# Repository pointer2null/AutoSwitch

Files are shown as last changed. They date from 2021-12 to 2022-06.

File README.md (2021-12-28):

# AutoSwitch

Auto switch to start a vac or dust collector when a tool starts.

Simple circuit based on the ATTiny85 PCU that monitors the current drawn by a tool, typically a wood working tool such as a saw or planer, and activates a dust collecter when that tool is switched on.

Current is sensed with the ACS712 hall device and the ATTiny85 samples this and after a short delay fires the triac, via an opto isolator, to power on the dust collector.

A seperate relay provides a volt free set of contacts in case blast gates need controlling.

There is a serial port which allows tweaking of the trigger values and time delays.

## Operation

The AtTiny85 uses it's onboard DAC to sample the analogue output from the hall sensor. If this value is above the adcThreshold value, a counter is incremented on each poll, up to the max counter value. If the hall value is below this threshold the counter is decremented. When the counter exceed the on count value and the hall value is above the threadhold, the output triac is switched on. When the count drops below the off count value and the hall value is below the threashold, the triac is switched off. To give a clean shutoff the count value is also set to zero at this point.

## Serial interface

A vac switch doesn't need a seial interface, but I was bored and it got one!

Use the default serial settings: 9600 baud, Data 8, Stop 1, no parity and Xon/Xoff.

A list of commands should be displayed.

- get          : get all config values
- current [n]  : get or set the tool current threshold value
- on [n]       : get or set the on trigger value
- off [n]      : get or set the off trigger value
- count [n]    : get or set the max count value
- period [n]   : get or set the poll period (ms)
- def          : set the default values
- cal          : auto set the current threshold
- watch        : watch the current system values (x to stop)
- fon|foff     : force switch on/off

These allow the internal values to be modified to tweak the behaviour. Values are store in the internal EEPROM.

The **on** value must always be greater than zero and less than the off value.

The **off** value must always be greater that the on value and less than the count max value.

The **count** value must always be greater than the off vlaue.

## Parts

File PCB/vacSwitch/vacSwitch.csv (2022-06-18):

Reference | Value | Footprint | Datasheet
U1 | ATtiny85-20PU | Package_DIP:DIP-8_W7.62mm_LongPads | http://ww1.microchip.com/downloads/en/DeviceDoc/atmel-2586-avr-8-bit-microcontroller-attiny25-attiny45-attiny85_datasheet.pdf
U2 | ACS712xLCTR-20A | Package_SO:SOIC-8_3.9x4.9mm_P1.27mm | http://www.allegromicro.com/~/media/Files/Datasheets/ACS712-Datasheet.ashx?la=en
R7 | 220R | Resistor_THT:R_Axial_DIN0207_L6.3mm_D2.5mm_P7.62mm_Horizontal | ~
R8 | 220R | Resistor_THT:R_Axial_DIN0207_L6.3mm_D2.5mm_P7.62mm_Horizontal | ~
R4 | 2K2 | Resistor_THT:R_Axial_DIN0207_L6.3mm_D2.5mm_P7.62mm_Horizontal | ~
D1 | 1N4148 | Diode_THT:D_DO-35_SOD27_P7.62mm_Horizontal | https://assets.nexperia.com/documents/data-sheet/1N4148_1N4448.pdf
C3 | 1nF | Capacitor_THT:CP_Radial_Tantal_D6.0mm_P5.00mm | ~
C4 | 10pF | Capacitor_THT:CP_Radial_Tantal_D5.0mm_P5.00mm | ~
R3 | 10K | Resistor_THT:R_Axial_DIN0207_L6.3mm_D2.5mm_P7.62mm_Horizontal | ~
C1 | 0.1uF | Capacitor_THT:CP_Radial_Tantal_D5.0mm_P5.00mm | ~
D6 | RED LED | LED_THT:LED_D3.0mm | ~
D7 | ORANGE LED | LED_THT:LED_D3.0mm | ~
Q1 | BC547 | Package_TO_SOT_THT:TO-92_Inline | https://www.onsemi.com/pub/Collateral/BC550-D.pdf
R9 | 220R | Resistor_THT:R_Axial_DIN0207_L6.3mm_D2.5mm_P7.62mm_Horizontal | ~
R10 | 1k | Resistor_THT:R_Axial_DIN0207_L6.3mm_D2.5mm_P7.62mm_Horizontal | ~
U3 | MOC3043M | Package_DIP:DIP-6_W7.62mm_LongPads | https://www.onsemi.com/pub/Collateral/MOC3043M-D.pdf
R12 | 360R | Resistor_THT:R_Axial_DIN0207_L6.3mm_D2.5mm_P7.62mm_Horizontal | ~
R11 | 330R | Resistor_THT:R_Axial_DIN0207_L6.3mm_D2.5mm_P7.62mm_Horizontal | ~
C6 | 0.047uF 47R | Capacitor_THT:C_Rect_L16.5mm_W7.0mm_P15.00mm_MKT | ~
D9 | MAC12MG | Package_TO_SOT_THT:TO-220-3_Vertical | ~
J2 | RS232 | Connector_JST:JST_PH_B3B-PH-K_1x03_P2.00mm_Vertical | ~
J3 | ISP | Connector_JST:JST_PH_B6B-PH-K_1x06_P2.00mm_Vertical | ~
J1 | Mains | Samsys:1729160 | ~
K1 | HE721A0510 | Relay_THT:Relay_StandexMeder_DIP_LowProfile | https://standexelectronics.com/wp-content/uploads/datasheet_reed_relay_DIP.pdf
J4 | VoltFreeContact | Connector_JST:JST_PH_B2B-PH-K_1x02_P2.00mm_Vertical | ~
PS1 | RAC04-05SGA | Converter_ACDC:Converter_ACDC_RECOM_RAC04-xxSGx_THT | https://www.recom-power.com/pdf/Powerline-AC-DC/RAC04-GA.pdf
RV1 | V250LA2P | Varistor:RV_Disc_D7mm_W3.9mm_P5mm | ~
JP1 | Program | Connector_PinHeader_2.54mm:PinHeader_1x03_P2.54mm_Vertical | ~

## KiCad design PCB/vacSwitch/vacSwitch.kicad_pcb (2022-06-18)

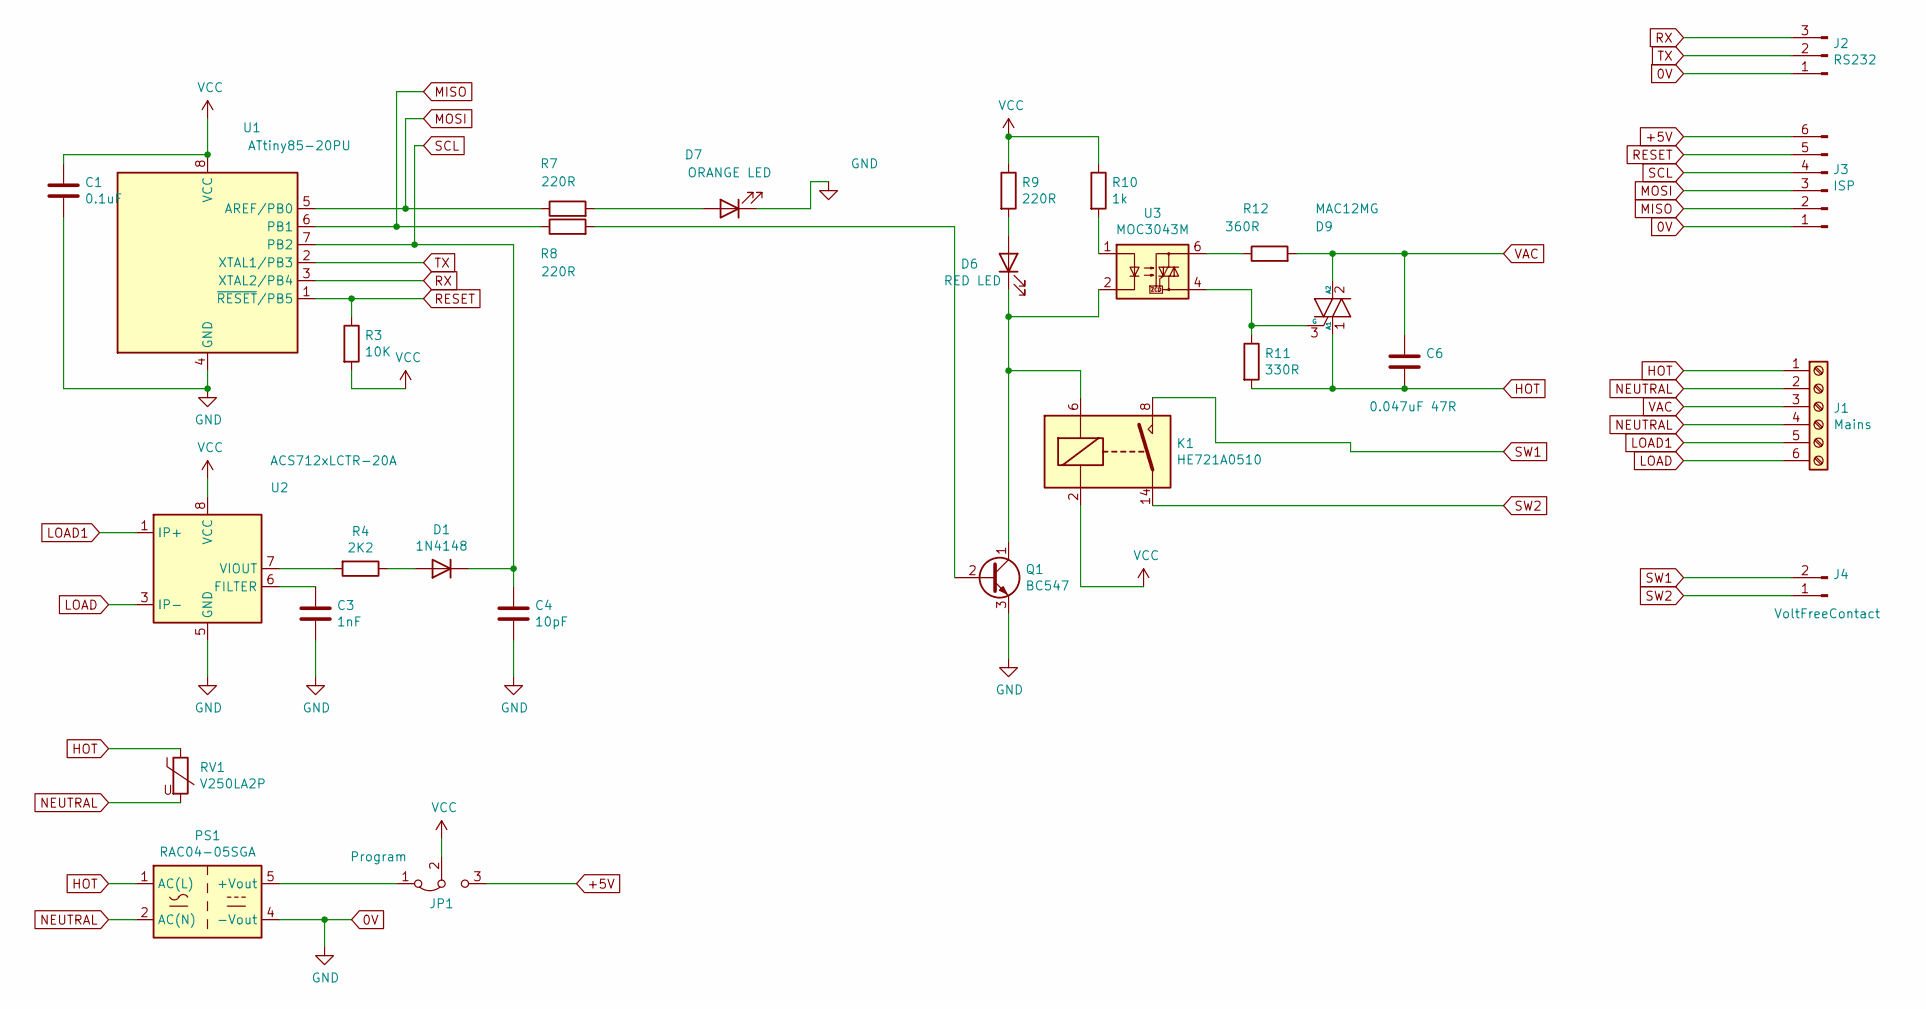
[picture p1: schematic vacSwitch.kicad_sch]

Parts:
C1: 0.1uF; CP_Radial_Tantal_D5.0mm_P5.00mm
C3: 1nF; CP_Radial_Tantal_D6.0mm_P5.00mm
C4: 10pF; CP_Radial_Tantal_D5.0mm_P5.00mm
C6: 0.047uF 47R; C_Rect_L16.5mm_W7.0mm_P15.00mm_MKT
D1: 1N4148; D_DO-35_SOD27_P7.62mm_Horizontal
D6: RED LED; LED_D3.0mm
D7: ORANGE LED; LED_D3.0mm
D9: MAC12MG; TO-220-3_Vertical
J1: Mains; 1729160
J2: RS232; JST_PH_B3B-PH-K_1x03_P2.00mm_Vertical
J3: ISP; JST_PH_B6B-PH-K_1x06_P2.00mm_Vertical
J4: VoltFreeContact; JST_PH_B2B-PH-K_1x02_P2.00mm_Vertical
JP1: Program; PinHeader_1x03_P2.54mm_Vertical
K1: HE721A0510; Relay_StandexMeder_DIP_LowProfile
PS1: RAC04-05SGA; Converter_ACDC_RECOM_RAC04-xxSGx_THT
Q1: BC547; TO-92_Inline
R3: 10K; R_Axial_DIN0207_L6.3mm_D2.5mm_P7.62mm_Horizontal
R4: 2K2; R_Axial_DIN0207_L6.3mm_D2.5mm_P7.62mm_Horizontal
R7, R8, R9: 220R; R_Axial_DIN0207_L6.3mm_D2.5mm_P7.62mm_Horizontal
R10: 1k; R_Axial_DIN0207_L6.3mm_D2.5mm_P7.62mm_Horizontal
R11: 330R; R_Axial_DIN0207_L6.3mm_D2.5mm_P7.62mm_Horizontal
R12: 360R; R_Axial_DIN0207_L6.3mm_D2.5mm_P7.62mm_Horizontal
RV1: V250LA2P; RV_Disc_D7mm_W3.9mm_P5mm
U1: ATtiny85-20PU; DIP-8_W7.62mm_LongPads
U2: ACS712xLCTR-20A; SOIC-8_3.9x4.9mm_P1.27mm
U3: MOC3043M; DIP-6_W7.62mm_LongPads

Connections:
0V: C1.2, C3.2, C4.2, D7.1 (K), J2.1, J3.1, PS1.4 (-Vout), Q1.3 (E), U1.4 (GND), U2.5 (GND)
+5V: J3.6, JP1.3 (B)
HOT: C6.2, D9.1 (A1), J1.1, PS1.1 (AC(L)), R11.2, RV1.1
LOAD: J1.6, U2.3 (IP-), U2.4 (IP-)
LOAD1: J1.5, U2.1 (IP+), U2.2 (IP+)
MISO: J3.2, R8.1, U1.6 (PB1)
MOSI: J3.3, R7.1, U1.5 (AREF/PB0)
NEUTRAL: J1.2, J1.4, PS1.2 (AC(N)), RV1.2
unnamed: C3.1, U2.6 (FILTER)
unnamed: D1.2 (A), R4.1
unnamed: D6.1 (K), K1.6, Q1.1 (C), U3.2
unnamed: D6.2 (A), R9.2
unnamed: D7.2 (A), R7.2
unnamed: D9.3 (G), R11.1, U3.4
unnamed: JP1.1 (A), PS1.5 (+Vout)
unnamed: Q1.2 (B), R8.2
unnamed: R4.2, U2.7 (VIOUT)
unnamed: R10.2, U3.1
unnamed: R12.1, U3.6
RESET: J3.5, R3.1, U1.1 (~RESET/PB5)
RX: J2.3, U1.3 (XTAL2/PB4)
SCL: C4.1, D1.1 (K), J3.4, U1.7 (PB2)
SW1: J4.2, K1.8
SW2: J4.1, K1.14
TX: J2.2, U1.2 (XTAL1/PB3)
VAC: C6.1, D9.2 (A2), J1.3, R12.2
VCC: C1.1, JP1.2 (C), K1.2, R3.2, R9.1, R10.1, U1.8 (VCC), U2.8 (VCC)

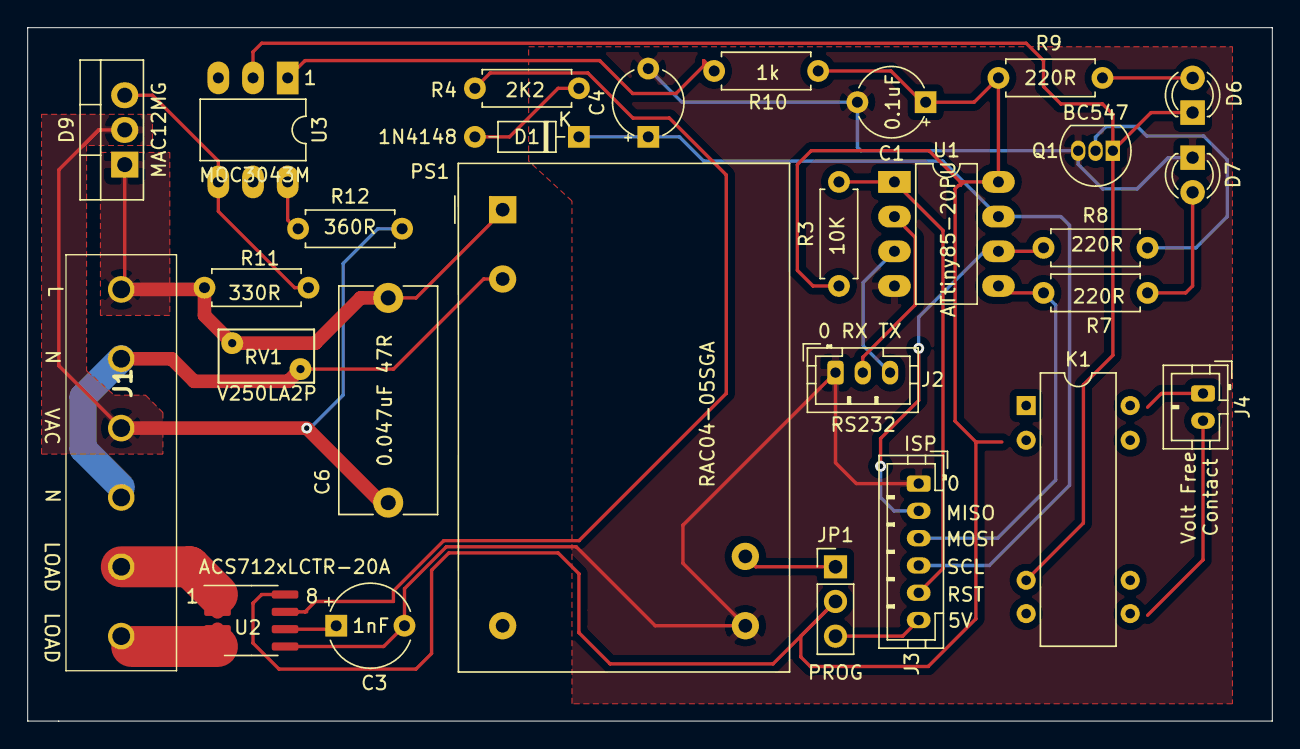
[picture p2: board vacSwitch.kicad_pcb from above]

Board: 2 copper layers, 91.2 x 50.8 mm, 28 parts (0 on the bottom side), 27 nets.

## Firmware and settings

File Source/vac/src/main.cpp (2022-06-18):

#include <vac.h>
#include <SoftwareSerial.h>
#include <EEPROM.h>
#include <Time.h>


int analogValue       = 0;             // hall sensor value
int thresholdCount    = 0;             // counter

boolean blink = false;
boolean watch = false;
boolean force = false;

long now           = 0;
long lastCheck     = 0;

bool blinkLed      = true;

char serial_command_buffer_[32];
struct Data {
  char magic[1];                       // need some way to see if the eeprom has been initialized
  int adcThreshold;                    // ADC current trigger level
  int thresholdCountMax;               // max counter value - affects how long we stay on after the tool is off
  int thresholdOn;                     // counter trigger level that turns on vac
  int thresholdOff;
  long checkPeriodMs;
};

Data d;

SoftwareSerial serial(serialRX, serialTX);
SerialCommands serial_commands_(&serial, serial_command_buffer_, sizeof(serial_command_buffer_), "\r", " ");

void valuesHeader() {
  serial.print(F("\r\n\nAnalog\tAnalog\t\tThreshold\tOn trigger\tOff trigger\tCounter"));
  serial.print(F("\r\nvalue\tthreshold\tcounter\t\tlevel\t\tlevel\t\tmax\r\n"));
}

void valuesDump() {
  serial.print(analogValue, DEC);
  serial.print(F("\t"));
  serial.print(d.adcThreshold, DEC);
  serial.print(F("\t\t"));
  serial.print(thresholdCount, DEC);
  serial.print(F("\t\t"));
  serial.print(d.thresholdOn, DEC);
  serial.print(F("\t\t"));
  serial.print(d.thresholdOff, DEC);
  serial.print(F("\t\t"));
  serial.print(d.thresholdCountMax, DEC);
  serial.print(F("\r\n"));
}


void useage() {
  serial.println(F("\r\n\n******GVac switch.******\r\n"));
  serial.println(F("get          : get all config values"));
  serial.println(F("current [n]  : get or set the tool current threshold value"));
  serial.println(F("on [n]       : get or set the on trigger value"));
  serial.println(F("off [n]      : get or set the off trigger value"));
  serial.println(F("count [n]    : get or set the max count value"));
  serial.println(F("period [n]   : get or set the poll period (ms)"));

  
  serial.println(F("def          : set the default values"));
  serial.println(F("cal          : auto set the current threshold"));
  serial.println(F("watch        : watch the current system values (x to stop)"));
  serial.println(F("f<on|off>    : force switch on/off"));
}

//*** seial commands ***
//Note: Commands are case sensitive

//This is the default handler, and gets called when no other command matches.
// note the F() macro stores the const strings in flash to same ram
void cmd_unrecognized(SerialCommands* sender, const char* cmd) {
  watch = false;
  sender->GetSerial()->print(F("Unrecognized command ["));
  sender->GetSerial()->print(cmd);
  sender->GetSerial()->println("]");
  useage();
}

//get command : display current settings
void cmd_get(SerialCommands* sender) {
  watch = false;
  valuesHeader();
  valuesDump();
  useage();
}
SerialCommand cmd_get_("get", cmd_get);

//set command : get/set the adc current threshold
void cmd_current(SerialCommands* sender) {
  watch = false;
  char* valStr = sender->Next();
  if (valStr == NULL) {
    sender->GetSerial()->print(F("Current sensor threshold: "));
    sender->GetSerial()->println(d.adcThreshold, DEC);
    useage();
    return;
  }

  int val = atoi(valStr);
  d.adcThreshold = val;
  EEPROM.put(0, d);
  valuesHeader();
  valuesDump();
  useage();
}
SerialCommand cmd_current_("current", cmd_current);


void cmd_period(SerialCommands* sender) {
  watch = false;
  char* valStr = sender->Next();
  if (valStr == NULL) {
    sender->GetSerial()->print(F("Loop period (ms): "));
    sender->GetSerial()->println(d.checkPeriodMs, DEC);
    useage();
    return;
  }

  int val = atoi(valStr);
  if (val < 1) {
    sender->GetSerial()->println(F("Nonsensical value - ignoring"));
  } else {
    d.checkPeriodMs = val;
    EEPROM.put(0, d);
  }
  valuesHeader();
  valuesDump();
  useage();
}
SerialCommand cmd_period_("current", cmd_period);


void cmd_count(SerialCommands* sender) {
  watch = false;
  char* valStr = sender->Next();
  if (valStr == NULL) {
    sender->GetSerial()->print(F("Count max: "));
    sender->GetSerial()->println(d.thresholdCountMax, DEC);
    useage();
    return;
  }

  int val = atoi(valStr);
  if (val <= d.thresholdOff) {
    sender->GetSerial()->println(F("Count max must be greater than the off threshold"));
  } else {
    d.thresholdCountMax = val;
    EEPROM.put(0, d);
  }
  valuesHeader();
  valuesDump();
  useage();
}
SerialCommand cmd_count_("count", cmd_count);

//called for watch command
void cmd_watch(SerialCommands* sender) {
  sender->GetSerial()->println(F("Current sensor values. "));
  sender->GetSerial()->println(F("** Press x to stop. **"));
  valuesHeader();
  watch = true;
}
SerialCommand cmd_watch_("watch", cmd_watch);

void cmd_stop_watch(SerialCommands* sender) {
  watch = false;
  useage();
}
SerialCommand cmd_stop_watch_("x", cmd_stop_watch, true);

void cmd_cal(SerialCommands* sender) {
  watch = false;
  sender->GetSerial()->println(F("calibrating: do not switch on load..."));
  int calVal = 0;
  unsigned long stopwatch = millis(); // Store a snapshot of the current time since the program started executing
  // Collect the max ADC value from the current sensor for the predetermined sample period
  while (millis() - stopwatch < calPeriodMs) {
    calVal = max(calVal, analogRead(sense));
    sender->GetSerial()->print(".");
    delay(250);
  }
  calVal += 20; // approx 200W
  sender->GetSerial()->print(F("\r\nComplete. New value is ["));
  sender->GetSerial()->print(calVal);
  sender->GetSerial()->println(F("]"));
  d.adcThreshold = calVal;
  EEPROM.put(0, d);
  valuesHeader();
  valuesDump();
  useage();
}
SerialCommand cmd_cal_("cal", cmd_cal);

void cmd_setOn(SerialCommands* sender) {
  watch = false;
  char* valStr = sender->Next();
  if (valStr == NULL) {
    sender->GetSerial()->print(F("Count on threshold: "));
    sender->GetSerial()->println(d.thresholdOn, DEC);
    useage();
    return;
  }

  int val = atoi(valStr);
  if (val <= 1 || val >= d.thresholdOff) {
    useage();
    return;
  }
  d.thresholdOn = val;
  EEPROM.put(0, d);
  valuesHeader();
  valuesDump();
  useage();
}
SerialCommand cmd_setOn_("on", cmd_setOn);

void cmd_setOff(SerialCommands* sender) {
  watch = false;
  char* valStr = sender->Next();
  if (valStr == NULL) {
    sender->GetSerial()->print(F("Count off threshold: "));
    sender->GetSerial()->println(d.thresholdOff, DEC);
    useage();
    return;
  }

  int val = atoi(valStr);
  if (val <= d.thresholdOn || val >= defaultThresholdCountMax) {
    useage();
    return;
  }
  d.thresholdOff = val;
  EEPROM.put(0, d);
  valuesHeader();
  valuesDump();
  useage();
}
SerialCommand cmd_setOff_("off", cmd_setOff);

void cmd_setDef(SerialCommands* sender) {
  setDefaults();
  valuesHeader();
  valuesDump();
  useage();
}
SerialCommand cmd_setDef_("def", cmd_setDef);

void cmd_setFOff(SerialCommands* sender) {
  force = false;
  valuesHeader();
  valuesDump();
  useage();
}
SerialCommand cmd_setFOff_("foff", cmd_setFOff);

void cmd_setFOn(SerialCommands* sender) {
  force = true;
  valuesHeader();
  valuesDump();
  useage();
}
SerialCommand cmd_setFOn_("fon", cmd_setFOn);


void setup() {
  serial.begin(9600);
  serial.print(F("\r\n******GVac switch.******\r\n"));
  useage();
  pinMode(sense, INPUT);
  pinMode(blinkPin, OUTPUT);
  pinMode(relay, OUTPUT);
  serial_commands_.SetDefaultHandler(cmd_unrecognized);
  serial_commands_.AddCommand(&cmd_current_);
  serial_commands_.AddCommand(&cmd_get_);
  serial_commands_.AddCommand(&cmd_watch_);
  serial_commands_.AddCommand(&cmd_stop_watch_);
  serial_commands_.AddCommand(&cmd_cal_);
  serial_commands_.AddCommand(&cmd_setOn_);
  serial_commands_.AddCommand(&cmd_setOff_);
  serial_commands_.AddCommand(&cmd_setDef_);
  serial_commands_.AddCommand(&cmd_setFOn_);
  serial_commands_.AddCommand(&cmd_setFOff_);
  serial_commands_.AddCommand(&cmd_period_);
  serial_commands_.AddCommand(&cmd_count_);

  // check eeprom - see if we've been initialized before
  EEPROM.get(0, d);
  if (d.magic[0] != 'G') {
    serial.print(F("First run, using defaults.\r\n"));
    // this is the first ever run
    // set defaults
    setDefaults();
  } else {
    serial.print(F("Program data loaded.\r\n"));
  }
  valuesHeader();
  valuesDump();
}

void setDefaults() {
  d.magic[0]          = 'G';
  d.thresholdCountMax = defaultThresholdCountMax;
  d.thresholdOn       = defaultThresholdOn;
  d.thresholdOff      = defaultThresholdOff;
  d.adcThreshold      = defaultCurrentThreshold;
  d.checkPeriodMs     = defaultCheckPeriodMs;
  EEPROM.put(0, d);
}

void loop() {
  now = millis();
  // check every 500ms
  if (force) {
    // set everything on
    digitalWrite(relay, HIGH);
    digitalWrite(blinkPin, HIGH);
  } else if (lastCheck + d.checkPeriodMs < now) {
    periodicCheck();
    lastCheck = now;
  }
  serial_commands_.ReadSerial();
}

void periodicCheck() {
  analogValue = analogRead(sense);
  if (watch) {
    valuesDump();
  }

  if ((analogValue >= d.adcThreshold) &&
      (thresholdCount <= d.thresholdCountMax)) {
    // switching on - over trigger level, increase counter
    //thresholdCount += d.thresholdRate;
    thresholdCount++;
    blink = true; // start blink to show tool is on
  }
  if ((analogValue < d.adcThreshold) && (thresholdCount > 0 )) {
    // current sense is below trigger
    blink = false;
    // count down slow
    thresholdCount--;
  }

  if ((thresholdCount > d.thresholdOn) && (analogValue > d.adcThreshold)) {
    // switch on
    thresholdCount = defaultThresholdCountMax;
    digitalWrite(relay, HIGH);
    digitalWrite(blinkPin, HIGH);
    blinkLed = true;
    blink = false; // cancel blink as we've switched on
  }

  if ((thresholdCount < d.thresholdOff) && (analogValue < d.adcThreshold)) {
    // switch off
    digitalWrite(relay, LOW);
    blink = false;
    blinkLed = false;
    // positive feedback for a clean switch off
    thresholdCount = 0;
  }
  if (blink) {
    blinkLed = !blinkLed;
  }

  digitalWrite(blinkPin, blinkLed);
}

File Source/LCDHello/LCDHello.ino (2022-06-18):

#include <LiquidCrystal_I2C.h>

// set the LCD number of columns and rows
int lcdColumns = 20;
int lcdRows = 4;

// set LCD address, number of columns and rows
// if you don't know your display address, run an I2C scanner sketch
LiquidCrystal_I2C lcd(0x27, lcdColumns, lcdRows);  

String messageStatic = "** Workshop Alarm **";
String messageToScroll = "Gary was here :)";

// Function to scroll text
// The function acepts the following arguments:
// row: row number where the text will be displayed
// message: message to scroll
// delayTime: delay between each character shifting
// lcdColumns: number of columns of your LCD
void scrollText(int row, String message, int delayTime, int lcdColumns) {
  for (int i=0; i < lcdColumns; i++) {
    message = " " + message;  
  } 
  message = message + " "; 
  for (int pos = 0; pos < message.length(); pos++) {
    lcd.setCursor(0, row);
    lcd.print(message.substring(pos, pos + lcdColumns));
    delay(delayTime);
  }
}

void setup(){
  // initialize LCD
  lcd.init();
  // turn on LCD backlight                      
  lcd.backlight();

  // set cursor to first column, first row
  lcd.setCursor(0, 0);
  // print static message
  lcd.print(messageStatic);
  
  lcd.setCursor(0, 2);
  // print static message
  lcd.print(messageStatic);
  
  lcd.setCursor(0, 3);
  // print static message
  lcd.print(messageStatic);
}

void loop(){
  // print scrolling message
  scrollText(1, messageToScroll, 250, lcdColumns);
  lcd.setCursor(0, 2);
}

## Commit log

2021-11-30 Move and added PCB
    [vacSwitch-B_Cu.gbr, vacSwitch-B_Mask.gbr, vacSwitch-B_Paste.gbr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]
2021-11-30 arduino needs the vac folder
2021-12-07 fixed the flashing led issue and a few more problems
    Serial values editor needs a tweak and so do the defaul values. On
    and off loginc may want a look as we stay on too long
2021-12-14 added force switch on and off
2021-12-14 update PCB (errors fixed)
    [vacSwitch-B_Cu.gbr, vacSwitch-B_Mask.gbr, vacSwitch-B_Paste.gbr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]
2021-12-14 missing files
    [vacSwitch.kicad_pcb]
2021-12-15 Board updates. V1.1
    [vacSwitch-B_Cu.gbr, vacSwitch-B_Mask.gbr, vacSwitch-B_Paste.gbr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]
2021-12-28 More serial and board tweaks
2022-06-18 Defaults tweak
    [vacSwitch.csv, vacSwitch.kicad_pcb, vacSwitch.kicad_sch]
